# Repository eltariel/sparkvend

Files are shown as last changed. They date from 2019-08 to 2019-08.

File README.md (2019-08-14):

# SparkVend
This is a collection of bits that allows a device to communicate with a vending machine that
implements the MDB/ICP standard.

## Ok, what?
At [SparkCC](https://sparkcc.org) we have a bunch of vending machines. Of these, at least one
talks MDB/ICP, which is a protocol that connects a VMC (vending machine controller) to a number
of devices, like coin mechs, bill acceptors, and cashless (credit card etc) devices. There's been
a long-standing project idea to actually *use* this vending machine, probably for common components
for projects, but managing money is a lot of effort and we could do it another way if we had the
interface.

So. I'm building one.

There's a lot of info floating around about how these things work, but I wanted to learn how to do
a heap of things, so I'm building it from scratch instead.

The biggest complication for this interface is the electronic interface - an opto-isolated
multidrop serial bus isn't a big deal on its own, but finding a UART that supports 9-bit
communications is a little less straightforward. A lot of microcontrollers have these, but then we
want to hook the vending machine to more powerful systems so we don't have to deal with low-level
considerations when we eventually build something way more complex than it needs to be.

Many of the design decisions for this project come from the contents of my gadget bin, as well as
my own abilities:
- MDB/ICP protocol implemented on a Teensy 3.x because I have spares
- Host system is (going to be) a Raspberry Pi because they're everywhere
- PCB design is mostly through-hole because I can just about manage to solder well enough for that

## Setup
This project has a bunch of filters defined to keep the KiCad files as git-friendly as possible. To
set this up correctly, run this:

    git config include.path ../extra.gitconfig

For more info about the filters, see [here](https://jnavila.github.io/plotkicadsch/).

## Repo Layout
### /
Contains project global stuff:
- This README
- Licensing info
- Additional git configuration

### /hardware
Schematics and PCB layouts for the board that connects all of the pieces together. Uses KiCad v5.

### /teensy
MDB/ICP interface firmware for the Teensy. This acts as MDB Cashless Device 1 (0x10). Uses
Teensyduino via PlatformIO, because the Arduino IDE is... weird.

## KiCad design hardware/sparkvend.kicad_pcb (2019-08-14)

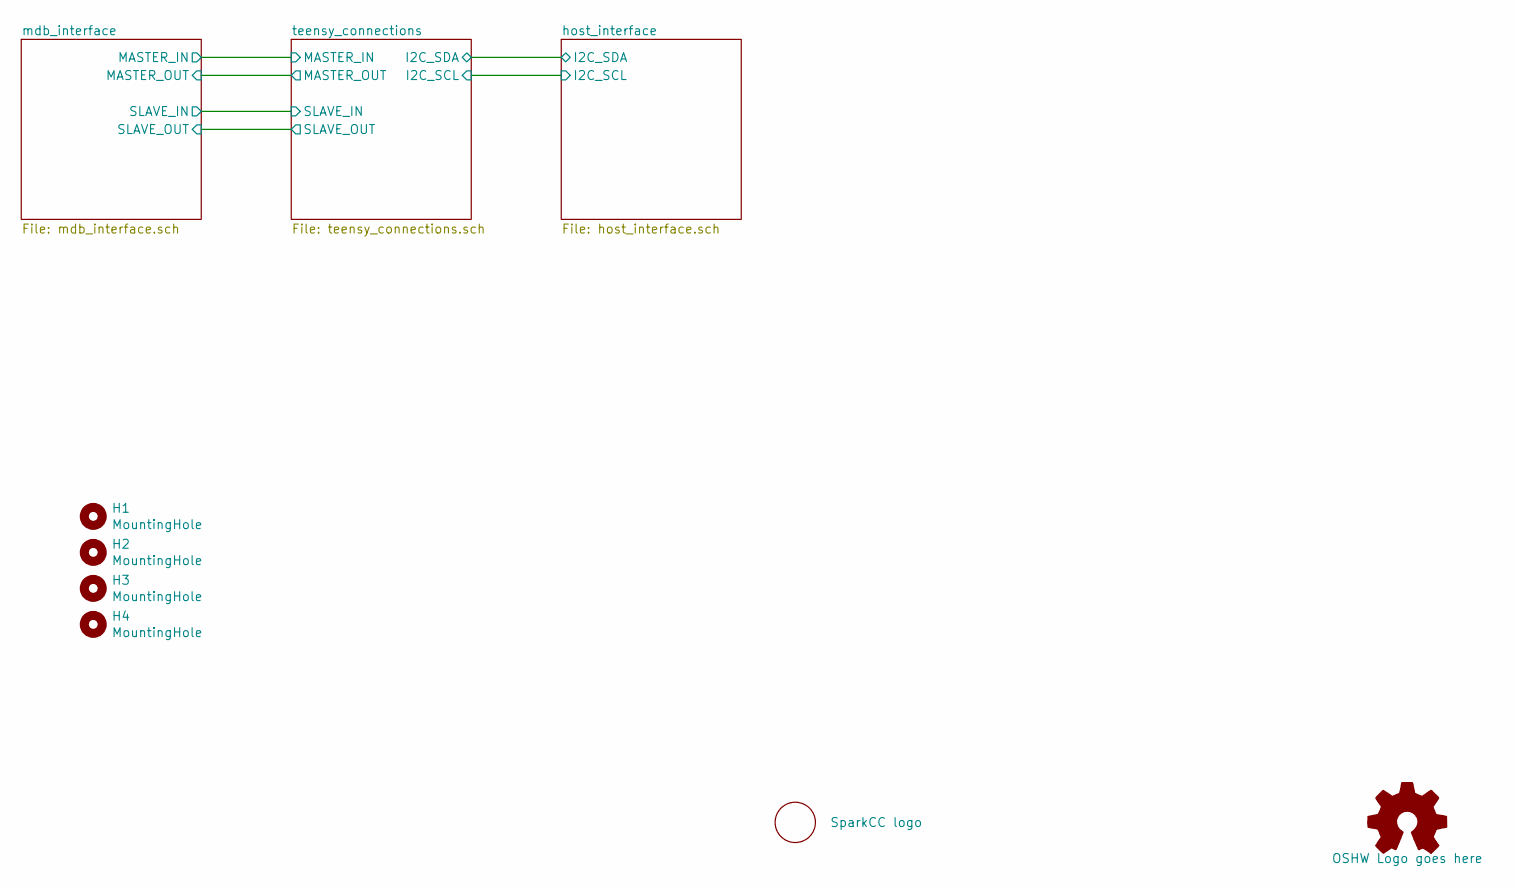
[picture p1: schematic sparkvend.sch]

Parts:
H1, H2, H3, H4: MountingHole; MountingHole_2.7mm_M2.5
LOGO1: SparkCC logo; SPARKCC_LOGO
LOGO3: OSHW Logo goes here; OSHW-Logo2_7.3x6mm_SilkScreen

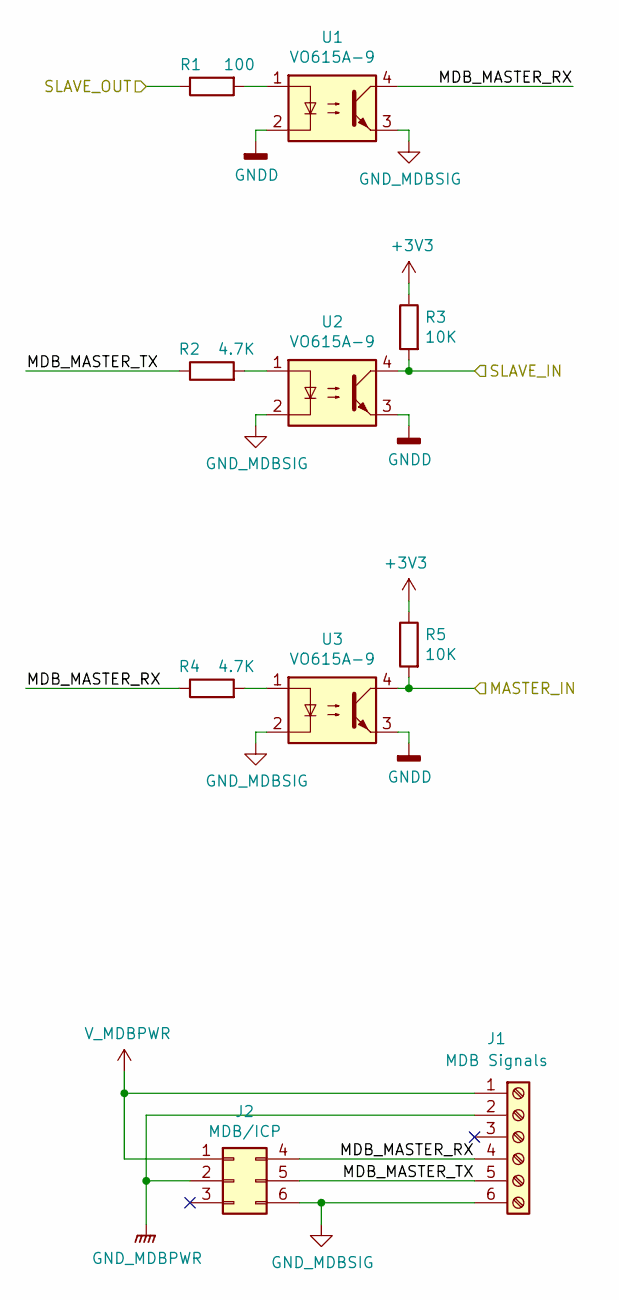
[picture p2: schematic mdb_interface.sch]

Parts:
J1: MDB Signals; SCREWTERMINAL-3.5MM-6
J2: MDB/ICP; Molex_Mini-Fit_Jr_5569-06A2_2x03_P4.20mm_Horizontal
R1: 100; R_Axial_DIN0207_L6.3mm_D2.5mm_P7.62mm_Horizontal
R2, R4: 4.7K; R_Axial_DIN0207_L6.3mm_D2.5mm_P7.62mm_Horizontal
R3, R5: 10K; R_Axial_DIN0207_L6.3mm_D2.5mm_P7.62mm_Horizontal
U1, U2, U3: VO615A-9; DIP-4_W7.62mm

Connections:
+3V3: R3.1, R5.1; also elsewhere on the board
/mdb_interface/MASTER_IN: R5.2, U3.4; also elsewhere on the board
/mdb_interface/MDB_MASTER_RX: J1.4, J2.4, R4.1, U1.4
/mdb_interface/MDB_MASTER_TX: J1.5, J2.5, R2.1
/mdb_interface/SLAVE_IN: R3.2, U2.4; also elsewhere on the board
/mdb_interface/SLAVE_OUT: R1.1; also elsewhere on the board
GNDD: U1.2, U2.3, U3.3; also elsewhere on the board
GNDMDB: J1.2, J2.2
GND_MDBSIG: J1.6, J2.6, U1.3, U2.2, U3.2
unnamed: R1.2, U1.1
unnamed: R2.2, U2.1
unnamed: R4.2, U3.1
V_MDBPWR: J1.1, J2.1

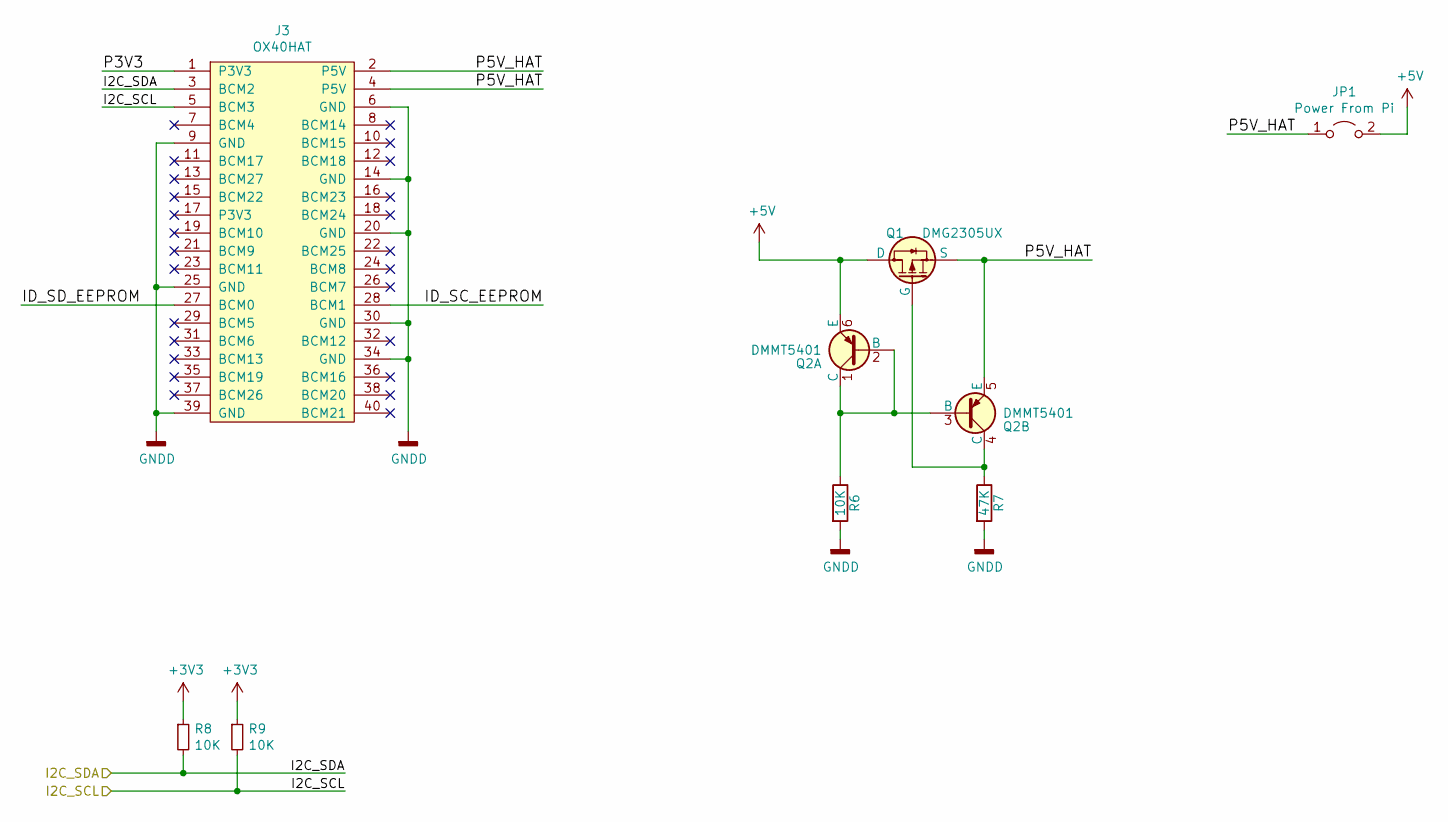
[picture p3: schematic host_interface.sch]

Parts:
J3: OX40HAT; PinSocket_2x20_P2.54mm_Vertical
JP1: Power From Pi; PinHeader_1x02_P2.54mm_Vertical
Q1: DMG2305UX; SOT-23
Q2: DMMT5401; SOT-23-6
R6: 10K; R_0603_1608Metric_Pad1.05x0.95mm_HandSolder
R7: 47K; R_0603_1608Metric_Pad1.05x0.95mm_HandSolder
R8, R9: 10K; R_Axial_DIN0207_L6.3mm_D2.5mm_P7.62mm_Horizontal

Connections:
+3V3: R8.1, R9.1; also elsewhere on the board
+5V: JP1.2 (B), Q1.3 (D), Q2.6 (E); also elsewhere on the board
/host_interface/I2C_SCL: J3.5 (BCM3), R9.2; also elsewhere on the board
/host_interface/I2C_SDA: J3.3 (BCM2), R8.2; also elsewhere on the board
/host_interface/ID_SC_EEPROM: J3.28 (BCM1)
/host_interface/ID_SD_EEPROM: J3.27 (BCM0)
/host_interface/P3V3: J3.1 (P3V3)
/host_interface/P5V_HAT: J3.2 (P5V), J3.4 (P5V), JP1.1 (A), Q1.2 (S), Q2.5 (E)
GNDD: J3.6 (GND), J3.9 (GND), J3.14 (GND), J3.20 (GND), J3.25 (GND), J3.30 (GND), J3.34 (GND), J3.39 (GND), R6.2, R7.2; also elsewhere on the board
unnamed: Q1.1 (G), Q2.4 (C), R7.1
unnamed: Q2.1 (C), Q2.2 (B), Q2.3 (B), R6.1

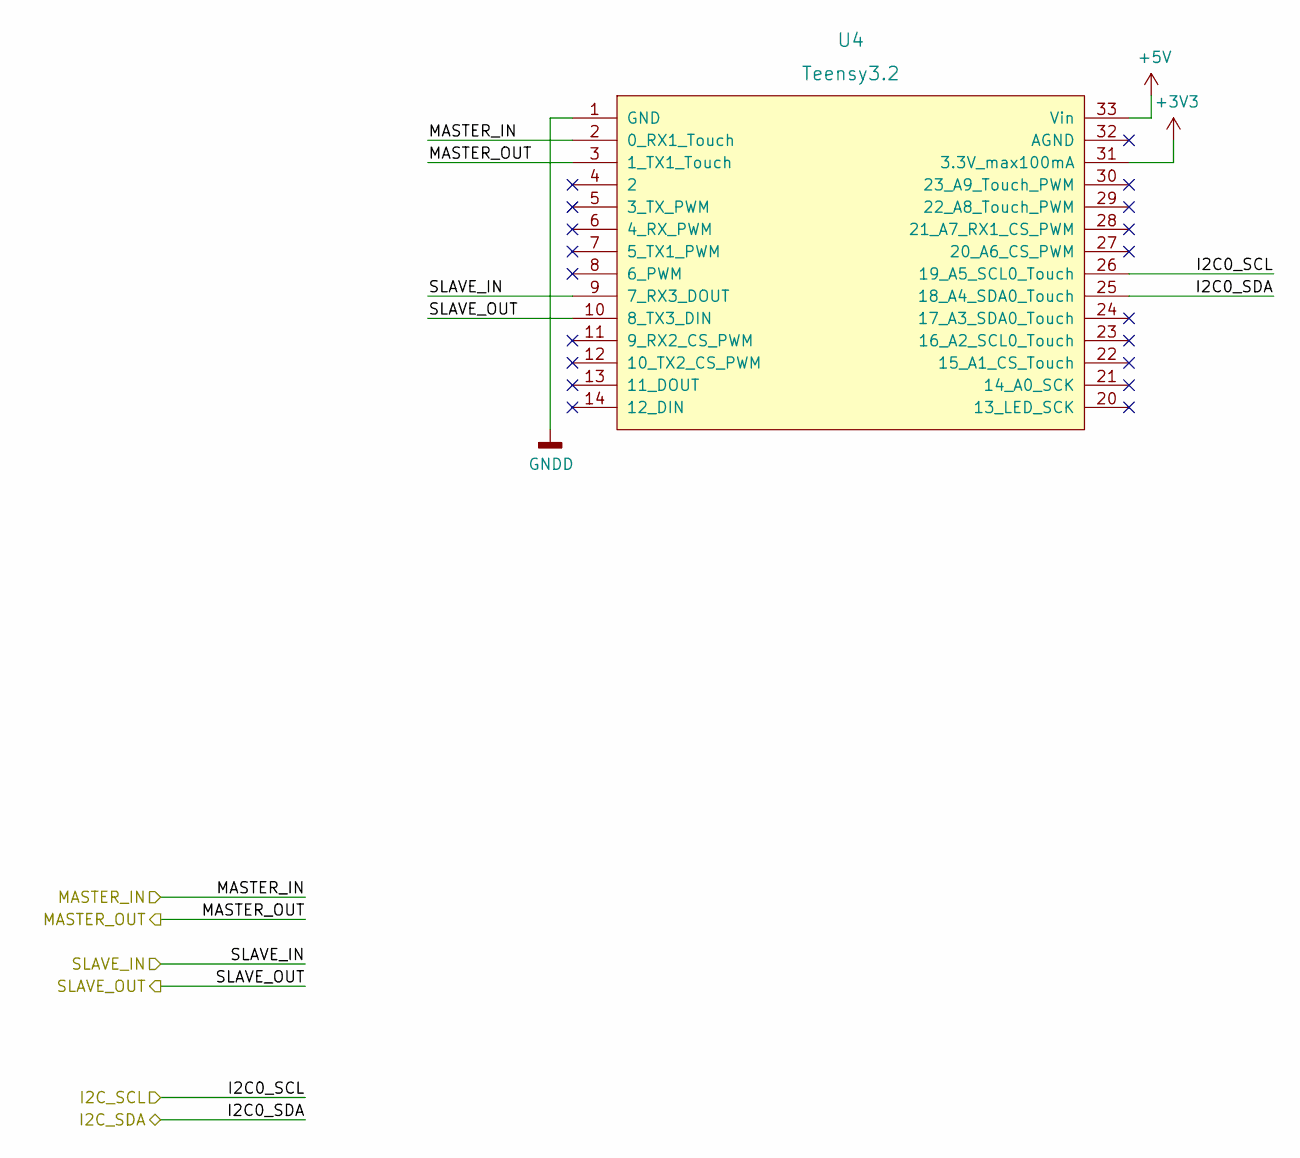
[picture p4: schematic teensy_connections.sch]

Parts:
U4: Teensy3.2; teensy-3.x-common

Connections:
+3V3: U4.31 (3.3V_max100mA); also elsewhere on the board
+5V: U4.33 (Vin); also elsewhere on the board
/host_interface/I2C_SCL: U4.26 (19_A5_SCL0_Touch); also elsewhere on the board
/host_interface/I2C_SDA: U4.25 (18_A4_SDA0_Touch); also elsewhere on the board
/mdb_interface/MASTER_IN: U4.2 (0_RX1_Touch); also elsewhere on the board
/mdb_interface/SLAVE_IN: U4.9 (7_RX3_DOUT); also elsewhere on the board
/mdb_interface/SLAVE_OUT: U4.10 (8_TX3_DIN); also elsewhere on the board
/teensy_connections/MASTER_OUT: U4.3 (1_TX1_Touch)
GNDD: U4.1 (GND); also elsewhere on the board

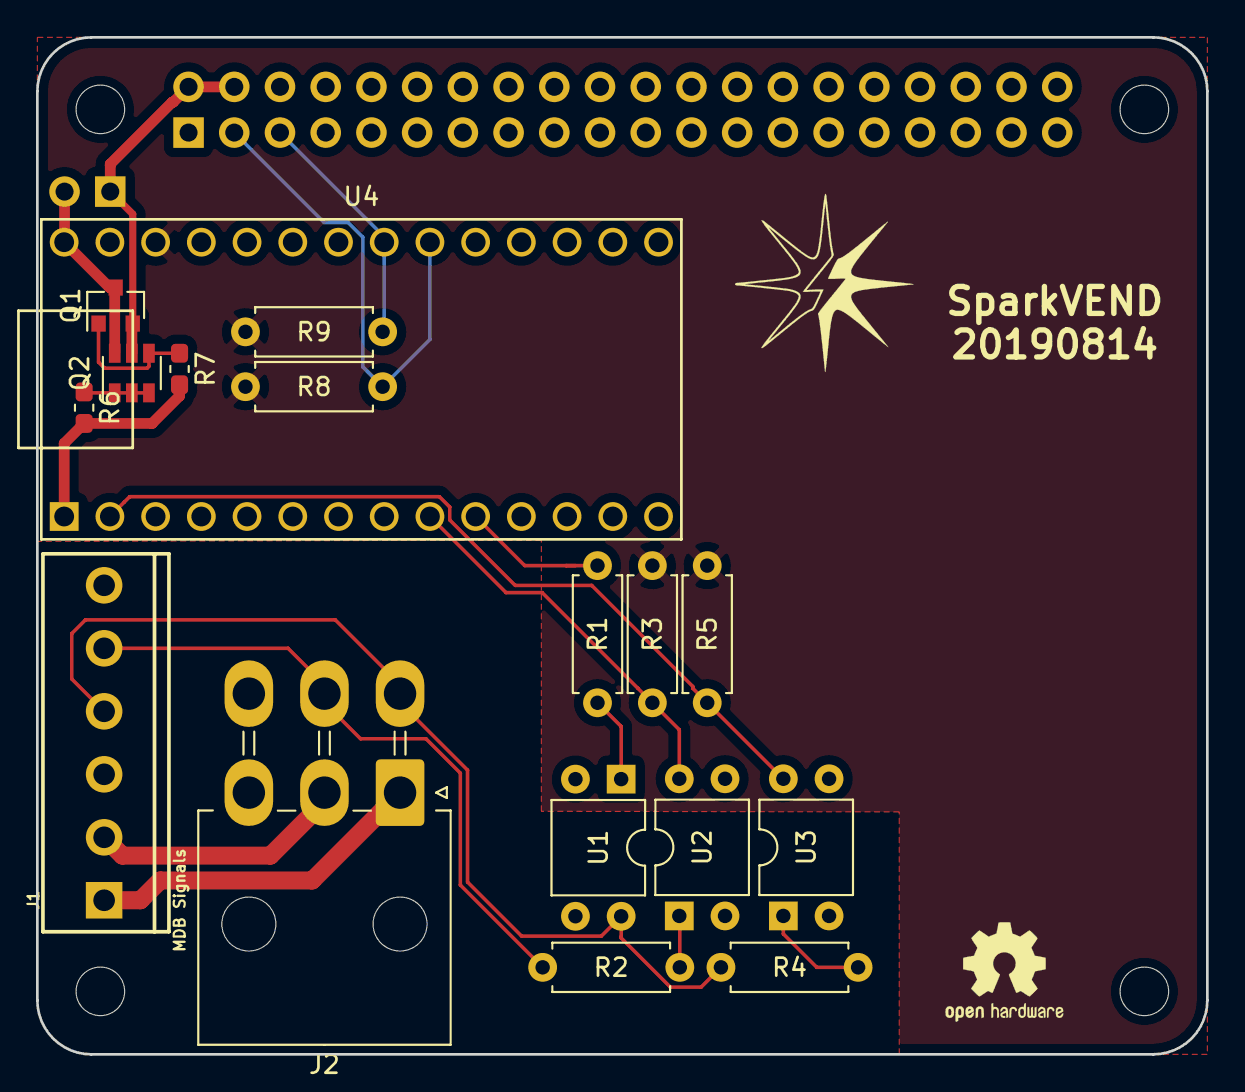
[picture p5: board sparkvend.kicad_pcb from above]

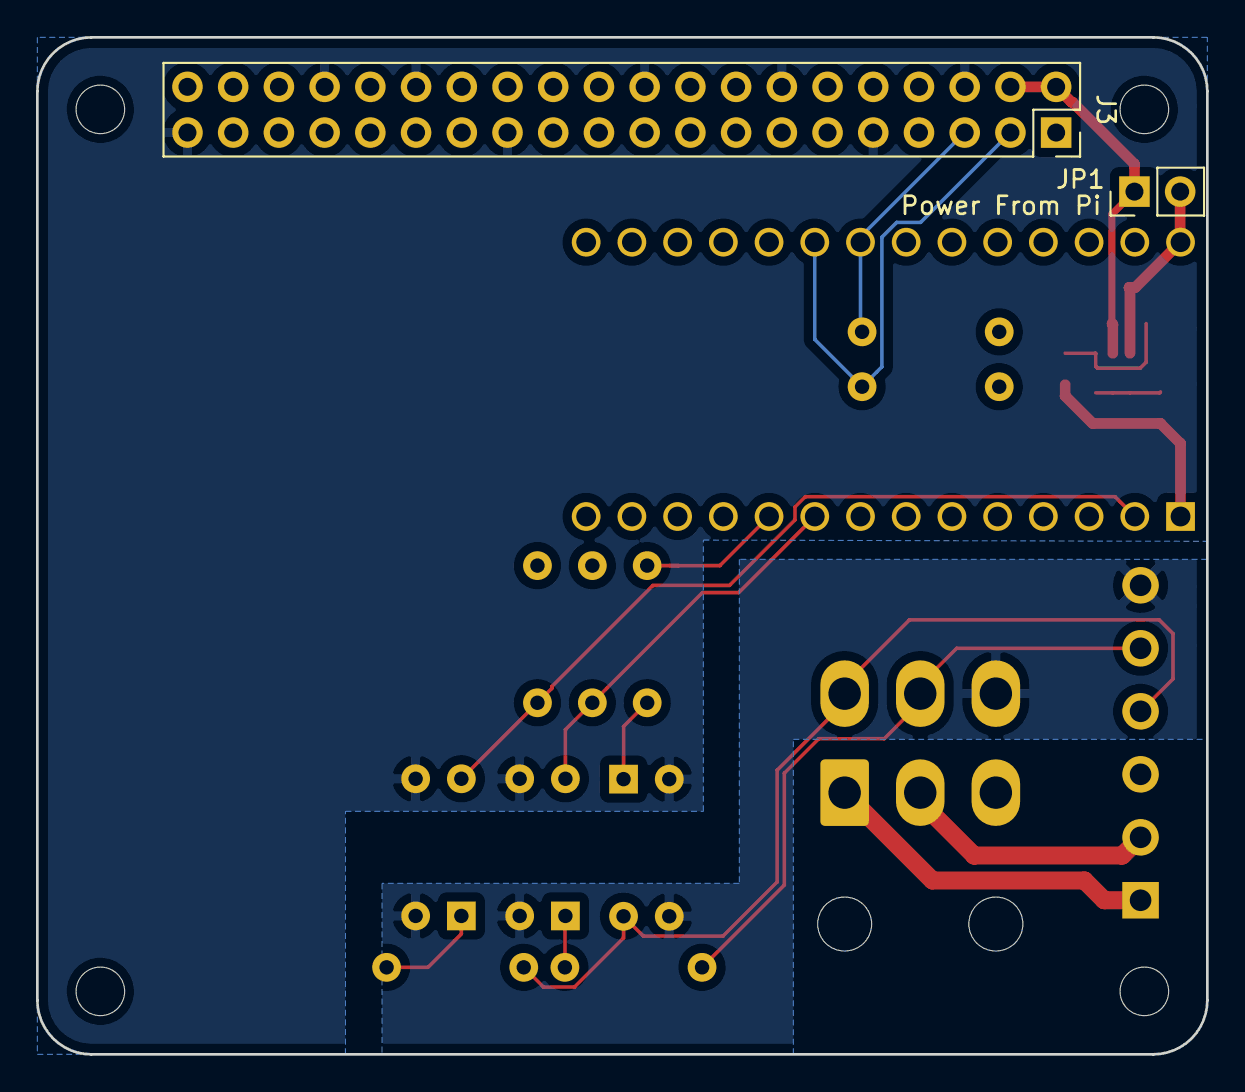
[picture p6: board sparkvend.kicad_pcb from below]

Board: 2 copper layers, 65.0 x 56.5 mm, 25 parts (2 on the bottom side), 19 nets.

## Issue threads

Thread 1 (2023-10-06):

Casheless device implementation

note5, 2023-10-06:
Hi and thank you for this repo.
Is it possible to get a more comprehensive explanation of the code. I have the teensy board and I can confirm it is parsing the 9bit data correctly now I am trying to understand your code structure and flow so that I can develop a cashless device. Any feedback from you is highly welcomed.

eltariel, 2024-01-08:
Hi @note5, apologies for the massive delay. $work has been busy and I've kind of abandoned this project since I no longer have access to any vending machines - you may have noticed that there's been no activity on this repo for ~5 years...

The teensy handles the MDB protocol on the `host` serial port, the `sniff` serial port is a read-only debugging aid to let me see what's happening on the MDB bus, and the usb serial is used for logging etc. It also acts as an i2c peripheral and exports a (very) limited command set to be used by a host device (i.e. raspberry pi) which is where the brains of the cashless device would sit.

The core MDB parsing is in `teensy/src/mdb_parse.cpp` which handles decoding the actual messages, and the cashless device implementation is in `teensy/src/mdb_cashless.cpp`. The parser uses "handlers" to allow it to be flexible about what commands it works with, these handlers are registered by passing the MDB command/subcommand pair to `mdb_register_handler()` along with a function to actually decode it.

The I2C interface is defined in `teensy/src/i2c_interface.cpp`, and it uses functions declared in the cashless device implementation to work with the device state. The i2c host app that ran on my pi is lost so I don't have a good example of how to use it.

Bear in mind that there's no guarantee any of this works properly - it's in a very early state, and MDB implementations have a long history of only vaguely adhering to the standards correctly. This did at least work well enough to add currency to our vending machine and allow us to dispense an item.

There's also an old kicad project in here which defines a hat that connects the i2c between a pi and a teensy, and has the necessary electronics to connect it all to MDB. It worked well enough at the time but I'm not sure how kicad would handle it now. I've got a pile of unpopulated boards floating around because I had to order a batch of 10 and only needed one 🤣

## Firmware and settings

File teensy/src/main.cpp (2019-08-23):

/**
 * Copyright 2019 Ellie Tomkins
 *
 * This file is part of SparkVend.
 *
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
 * You should have received a copy of the GNU General Public License
 * along with SparkVend.  If not, see <https://www.gnu.org/licenses/>.
 */

#include <Arduino.h>
#include <HardwareSerial.h>
#include <Wire.h>

#include <mdb_defs.h>
#include <mdb_parse.h>
#include <mdb_cashless.h>

#include <i2c_interface.h>

const int led_pin = 13;

HardwareSerial *peripheral = &Serial3;
HardwareSerial *sniff = &Serial1;
usb_serial_class *host = &Serial;

size_t tx(uint16_t data)
{
    return peripheral->write9bit(data);
}

void log(const char* msg)
{
    host->print(msg);
}

void setup()
{
    pinMode(led_pin, OUTPUT);

    host->begin(9600);
    sniff->begin(9600, SERIAL_9N1);
    peripheral->begin(9600, SERIAL_9N1_TXINV);

    i2c_setup();
    
    mdb_parser_init(&tx, host);
    mdb_cashless_init(host);
}

uint8_t current_addr = 0;
void dump_incoming(uint16_t incoming)
{
    host->print(">>> ");

    if (incoming & MDB_MODE_BIT)
    {
        current_addr = MDB_ADDRESS_MASK & incoming;
        
        switch (current_addr)
        {
        case MDB_ADDR_CHANGER:
            host->print("COINMECH       ");
            break;
        case MDB_ADDR_CASHLESS1:
            host->print("CASHLESS       ");
            break;
        case MDB_ADDR_BILLVALIDATOR:
            host->print("BILL VALIDATOR ");
            break;
        default:
            host->print("UNKNOWN        ");
            break;
        }
    }
    else
    {
        host->print("               ");
    }
    
    host->print(" 0x");
    host->print(incoming, HEX);
    host->print(" 0b");
    host->println(incoming, BIN);
}

void loop()
{
    int pin_state = HIGH;
    int incoming;

    if (peripheral->available() > 0)
    {
        incoming = peripheral->read();
        digitalWrite(led_pin, pin_state);
        pin_state = (pin_state == HIGH) ? LOW : HIGH;
        // dump_incoming(incoming);

        mdb_parse(incoming);
    }

    if (sniff->available() > 0)
    {
        incoming = sniff->read();
        host->print("TO VMC:   ");
        host->println(incoming, HEX);
    }
}

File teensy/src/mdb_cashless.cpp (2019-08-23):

/**
 * Copyright 2019 Ellie Tomkins
 *
 * This file is part of SparkVend.
 *
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
 * You should have received a copy of the GNU General Public License
 * along with SparkVend.  If not, see <https://www.gnu.org/licenses/>.
 */

#include <mdb_defs.h>
#include <mdb_parse.h>
#include <mdb_cashless.h>

#include <string.h>

static Print* l;
#define CASHLESS_LOG "[cashless]  "
#define LOG(str) (l->println(CASHLESS_LOG str))
#define LOGF(str,...) (l->printf(CASHLESS_LOG str, __VA_ARGS__))

#ifdef VERBOSE_LOGGING
    #define SPAM(str) (l->println(PARSE_LOG str))
    #define SPAMF(str,...) (l->printf(PARSE_LOG str, __VA_ARGS__))
#else
    #define SPAM(str)
    #define SPAMF(str,...)
#endif

static uint8_t cashless_state = MDB_CASHLESS_STATE_INACTIVE;
static bool has_config = false;
static bool has_prices = false;
static bool reset_session = false;
static bool disable_after_vend = false;

static struct mdb_cashless_config_cmd vmc_config;
static struct mdb_cashless_config_response my_config = {
    0x01,   // Feature level 1
    0x1036, // AUD
    2,      // Scale factor
    2,      // Decimal places
    10,     // Max response time (s)
    0b00000110    // L1 option bits: multivend capable, has display.
};

static const char* state_labels[] =
{
    "INACTIVE",
    "DISABLED",
    "ENABLED",
    "IDLE",
    "VEND",
    "REVALUE",
    "NEGVEND",
};

static uint16_t available_funds = 0;
static uint8_t vend_count = 0;
static uint16_t last_item = 0;
static uint16_t last_price = 0;

void mdb_cashless_funds_available(uint16_t funds)
{
    available_funds = funds;
    reset_session = true;
}

uint8_t mdb_cashless_get_current_state()
{
    return cashless_state;
}

uint8_t mdb_cashless_get_vend_count()
{
    return vend_count;
}

uint16_t mdb_cashless_get_current_funds()
{
    return available_funds;
}

uint16_t mdb_cashless_get_last_item()
{
    return last_item;
}

uint16_t mdb_cashless_get_last_price()
{
    return last_price;
}

static uint8_t set_state(uint8_t new_state)
{
    if(new_state == cashless_state) return cashless_state;

    if((cashless_state == MDB_CASHLESS_STATE_INACTIVE && !(new_state == MDB_CASHLESS_STATE_DISABLED)) ||
       (cashless_state == MDB_CASHLESS_STATE_DISABLED && !(new_state == MDB_CASHLESS_STATE_INACTIVE ||
                                                           new_state == MDB_CASHLESS_STATE_ENABLED)) ||
       (cashless_state == MDB_CASHLESS_STATE_ENABLED  && !(new_state == MDB_CASHLESS_STATE_INACTIVE ||
                                                           new_state == MDB_CASHLESS_STATE_DISABLED ||
                                                           new_state == MDB_CASHLESS_STATE_IDLE)) ||
       (cashless_state == MDB_CASHLESS_STATE_IDLE     && !(new_state == MDB_CASHLESS_STATE_INACTIVE ||
                                                           new_state == MDB_CASHLESS_STATE_DISABLED ||
                                                           new_state == MDB_CASHLESS_STATE_ENABLED ||
                                                           new_state == MDB_CASHLESS_STATE_VEND)) ||
       (cashless_state == MDB_CASHLESS_STATE_VEND     && !(new_state == MDB_CASHLESS_STATE_INACTIVE ||
                                                           new_state == MDB_CASHLESS_STATE_IDLE)) ||
        0)
    {
        LOGF("Invalid state transition: %s to %s\n", state_labels[cashless_state], state_labels[new_state]);
    }
    else
    {
        LOGF("Changing state from %s to %s\n", state_labels[cashless_state], state_labels[new_state]);
        cashless_state = new_state;
    }

    return cashless_state;
}

uint8_t test(uint8_t* rx, uint8_t* tx)
{
    tx[0] = MDB_NCK;
    return 0;
}

uint8_t mdb_cashless_ackonly(uint8_t* tx)
{
    tx[0] = MDB_ACK;
    return 0;
}

uint8_t mdb_cashless_out_of_sequence(uint8_t* tx)
{
    tx[0] = MDB_RESPONSE_OUTOFSEQ;
    return 1;
}

uint8_t mdb_cashless_reset(uint8_t* rx, uint8_t* tx)
{
    LOG("Reset\n");
    set_state(MDB_CASHLESS_STATE_INACTIVE);
    has_config = false;
    has_prices = false;

    return mdb_cashless_ackonly(tx);
}

uint8_t mdb_cashless_setup_config(uint8_t* rx, uint8_t* tx)
{
    has_config = true;

    set_state(has_prices ? MDB_CASHLESS_STATE_DISABLED : MDB_CASHLESS_STATE_INACTIVE);
    memcpy(&vmc_config, rx + 2, sizeof(vmc_config));

    for(int i = 0; i < 6; ++i)
    {
        l->printf("0x%02X ", rx[i]);
    }
    l->println("");

    LOGF("Config data received:\n\tfeature level %d, %dRx%dC, display type %d\n",
                            vmc_config.feature_level,
                            vmc_config.rows,
                            vmc_config.columns,
                            vmc_config.display_info);

    tx[0] = MDB_RESPONSE_READERCFG;
    memcpy(tx + 1, &my_config, sizeof(my_config));
    return 8;
}

uint8_t mdb_cashless_setup_prices(uint8_t* rx, uint8_t* tx)
{
    has_prices = true;

    LOG("OH MY GAWD I HAVE PRICE DATA\n");
    for(int i = 0; i < 6; ++i)
    {
        l->printf("0x%02X ", rx[i]);
    }
    LOG("");

    set_state(has_config ? MDB_CASHLESS_STATE_DISABLED : MDB_CASHLESS_STATE_INACTIVE);
    return mdb_cashless_ackonly(tx);
}

uint8_t mdb_cashless_poll_handler(uint8_t* rx, uint8_t* tx)
{
    SPAM("Poll!");
    uint8_t len = 0;
    if(cashless_state == MDB_CASHLESS_STATE_INACTIVE)
    {
        LOG("Poll: sending JUST RESET");
        tx[0] = MDB_RESPONSE_JUSTRESET;
        len = 1;
    }
    else if(cashless_state == MDB_CASHLESS_STATE_ENABLED && available_funds > 0)
    {
        LOG("Starting new session.");
        tx[0] = MDB_RESPONSE_NEWSESSION;
        memcpy(&tx[1], &available_funds, sizeof(available_funds));
        len = 3;
    }
    else if(cashless_state == MDB_CASHLESS_STATE_IDLE && reset_session)
    {
        LOG("Requesting session end.");
        tx[0] = MDB_RESPONSE_CANCELSESSION;
        len = 1;
    }
    else
    {
        len = mdb_cashless_ackonly(tx);
    }

    return len;
}

uint8_t mdb_cashless_reader_disable(uint8_t* rx, uint8_t* tx)
{
    if(cashless_state != MDB_CASHLESS_STATE_VEND)
    {
        LOG("Disabling reader.");
        set_state(MDB_CASHLESS_STATE_DISABLED);
    }
    else
    {
        LOG("Disabling reader after vend session.");
        disable_after_vend = true;
    }
    
    return mdb_cashless_ackonly(tx);
}

uint8_t mdb_cashless_reader_enable(uint8_t* rx, uint8_t* tx)
{
    uint8_t len = 0;
    if(cashless_state == MDB_CASHLESS_STATE_DISABLED && has_config && has_prices)
    {
        LOG("Enabling reader.");
        set_state(MDB_CASHLESS_STATE_ENABLED);
        disable_after_vend = false;

        len = mdb_cashless_ackonly(tx);
    }
    else
    {
        LOGF("Attempted to enable reader in incorrect state {0}\n", state_labels[cashless_state]);
        len = mdb_cashless_out_of_sequence(tx);
    }
    
    return len;
}
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

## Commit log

2019-08-14 PCB, licensing
    [host_interface.sch, mdb_interface.sch, sparkvend.kicad_pcb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]
2019-08-17 Enough protocol to allow vending!
    - Cashless init works correctly
    - When in the Enabled state, every poll will start a vend session
    - Also, minor log changes
    [mdb_cashless.cpp, mdb_parse.cpp]
2019-08-23 Added I2C interface

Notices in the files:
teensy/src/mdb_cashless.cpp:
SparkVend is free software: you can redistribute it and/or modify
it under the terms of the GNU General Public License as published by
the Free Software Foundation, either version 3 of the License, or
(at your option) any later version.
